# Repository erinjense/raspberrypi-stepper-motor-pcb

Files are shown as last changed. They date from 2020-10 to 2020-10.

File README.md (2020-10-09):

# Quad Stepper Motor Driver, Printed Circuit Board

## Disclaimer

This repository, "raspberrypi-stepper-motor-pcb", includes Open Source Hardware "DESGIN FILES AND GUIDES".

THE "DESIGN FILES AND GUIDES" ARE PROVIDED “AS IS”, WITHOUT WARRANTY OF ANY KIND, EXPRESS OR IMPLIED, INCLUDING BUT NOT LIMITED TO THE WARRANTIES OF MERCHANTABILITY, FITNESS FOR A PARTICULAR PURPOSE AND NONINFRINGEMENT. IN NO EVENT SHALL THE AUTHORS OR COPYRIGHT HOLDERS BE LIABLE FOR ANY CLAIM, DAMAGES OR OTHER LIABILITY, WHETHER IN AN ACTION OF CONTRACT, TORT OR OTHERWISE, ARISING FROM, OUT OF OR IN CONNECTION WITH THE "DESIGN FILES AND GUIDES" OR THE USE OR OTHER DEALINGS IN THE "DESIGN FILES AND GUIDES".

See [LICENSE](./LICENSE.md) for further details.

NOTE: This is not a Raspberry Pi "HAT" (Hardware Attached Top). A Raspberry Pi "HAT" is a specification by the Raspberry Pi Foundation set out to ensure various modules designed to interface with the Raspberry Pi do not conflict with each other. It is up to the User to ensure that the GPIO pins within this PCB module does not conflict with other modules, "HAT"s or desired use-cases.

See more within: [Raspberry Pi HAT Details](https://github.com/raspberrypi/hats)

This device is under test and not guaranteed to operate within electrical specifications or desired functionality.

##  Device Overview

### Features
✔️ Interfaces to Raspberry Pi, single-board computer, 40W GPIO Connector.

✔️ Drives up to 4 Stepper Motors.

✔️ Step Mode Control Switches.
 - Full, 1/2, 1/4, and 1/8

✔️ Motor Drive Current Limiting Potentiometers.

✔️ Mixed Decay Mode.

✔️ Minimal Raspberry Pi GPIO Pin Usage
-  Pins: 11, 13, 15, 29, 31 

✔️ DC Barrel Jack for commonly available power supplies.

### Electrical Specifications
✔️ VM Motor Power Supply (DC barrel jack): 8 ~ 32V

✔️ Continuous Motor Output Current: 0 ~ 1.5 A / Motor Set

✔️ Working Temperature: TBD

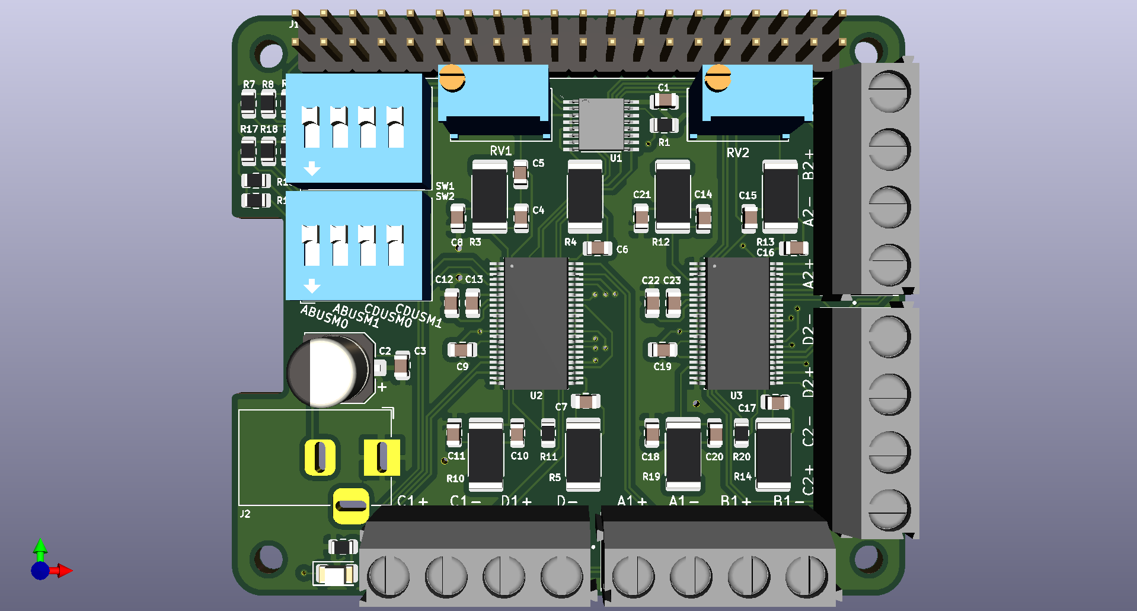
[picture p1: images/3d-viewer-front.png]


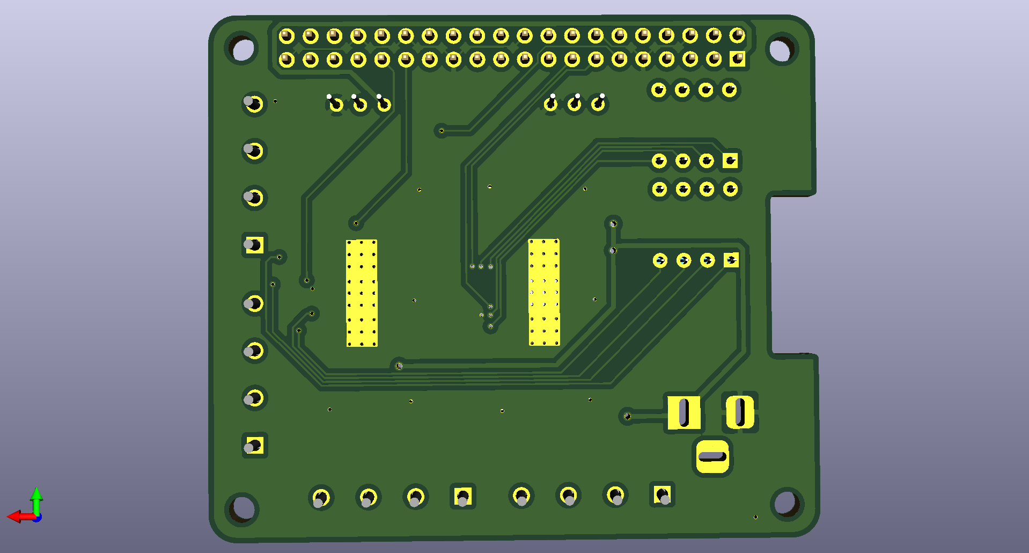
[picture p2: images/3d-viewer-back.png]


## Guides
- [Motor Selection](#motor-selection-guide)
- [Device Operation](#device-operation-guide)
- [Ordering PCB](#jlcpcb-order-guide)

## Motor Selection Guide
Coming soon...

## Device Operation Guide
Coming soon...

## Ordering Guide
This order guide covers the following:

- Purchasing printed circuit boards from JLCPCB with SMT assembly.
- Ordering remaining, through-hole, components from LCSC.

### Step 1: Upload Gerber Files
 - Download or clone this repository onto your computer.
 - Go to [JLCPCB.com](https://jlcpcb.com/)
 - Select "Quote Now" on the right-hand of JLCPCB.

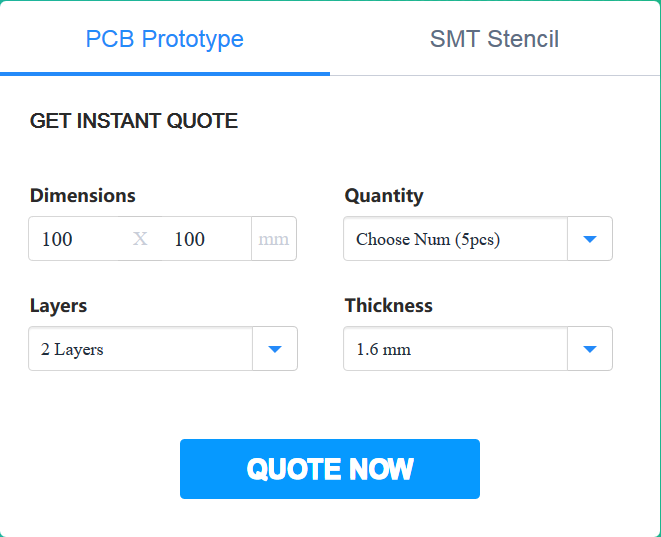
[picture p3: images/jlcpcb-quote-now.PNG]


- Select "Add your gerber file" on JLCPCB.
- Locate the "gerber" directory within this repository on your computer.
- Select and upload "gerber.zip".

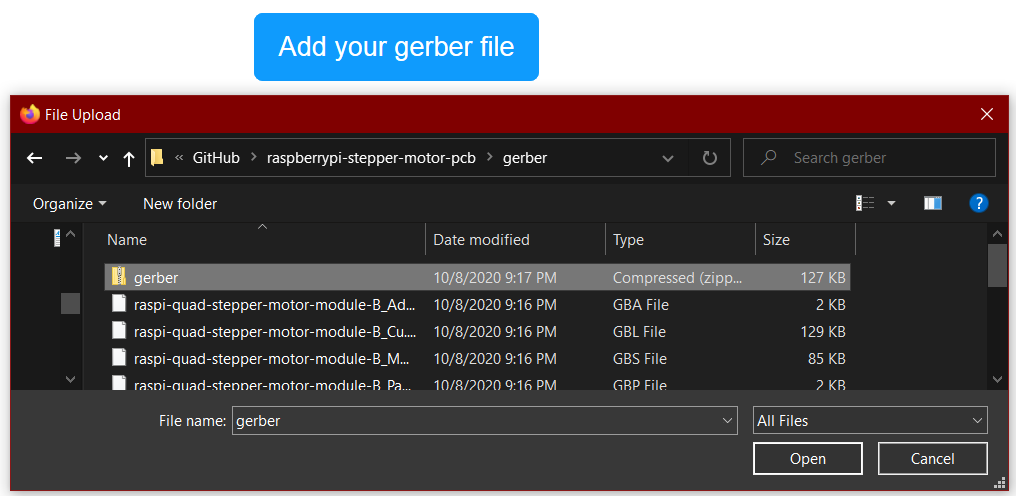
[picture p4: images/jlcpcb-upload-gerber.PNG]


### Step 2: Confirm PCB Specifications
- Confirm the following optional PCB specifications:
    - PCB Qty
    - Surface Finish (Lead-Free is extra money, but I chose this option.)
- Leave remaining options default unless you have a reason to change.

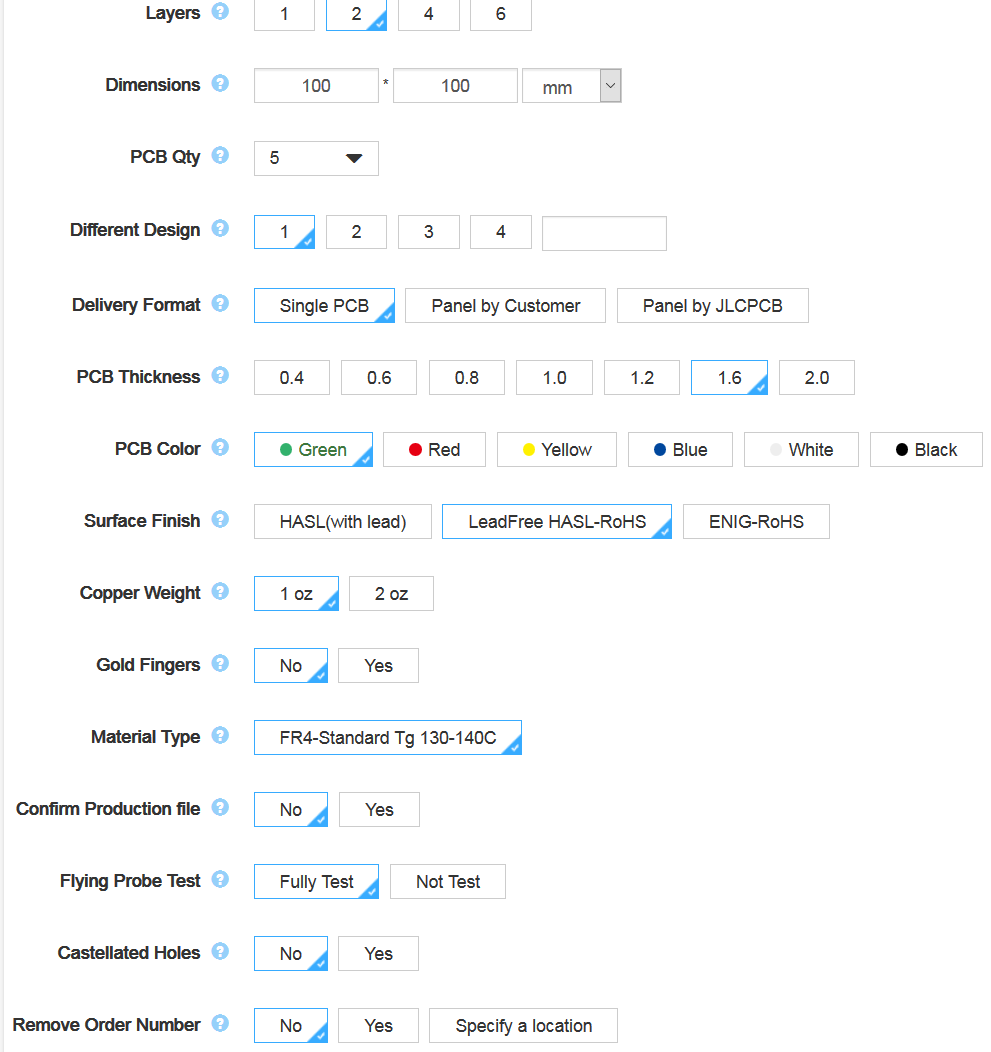
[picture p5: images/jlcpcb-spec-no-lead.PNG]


### Step 3: Optional SMT Assembly
- Toggle "SMT Assembly" option.
- Select "Assemble top side".
- Select your "SMT Qty" preference. (5 vs. 2)
- Leave Tooling holes as: "Added by JLCPCB".
- Click "Confirm".

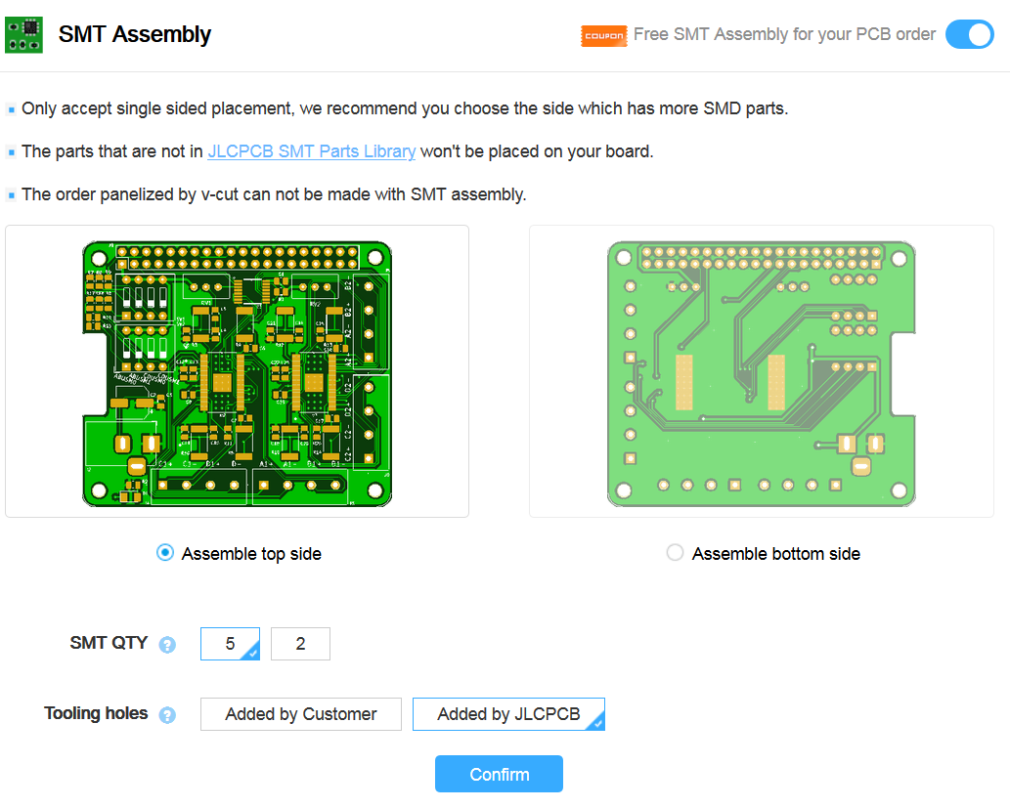
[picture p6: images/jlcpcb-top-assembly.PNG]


- ### Upload BOM and CPL
    - Click "Add BOM File".
    - Go to the "assembly" directory within the repository location on your computer.
    - Select "raspi-quad-stepper-motor-module_bom_jlc.csv"
    - Click "Add CPL File".
    - Go to the "assembly" directory within the repository location on your computer.
    - Select "raspi-quad-stepper-motor-module_cpl_jlc.csv"

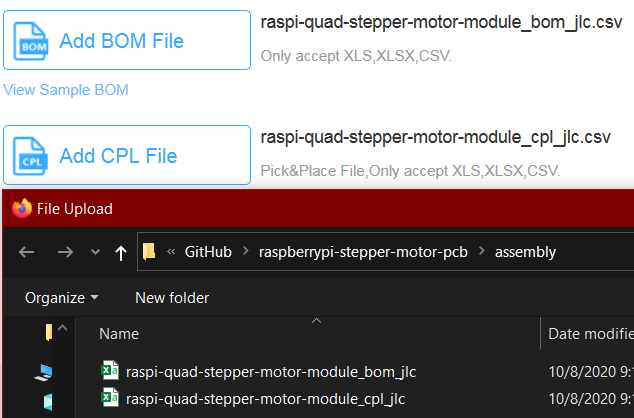
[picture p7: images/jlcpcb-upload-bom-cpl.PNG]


### Step 4: Review Charge Details
- If you chose "SMT assembly" you will see the SMT devices that will be populated on the boards.

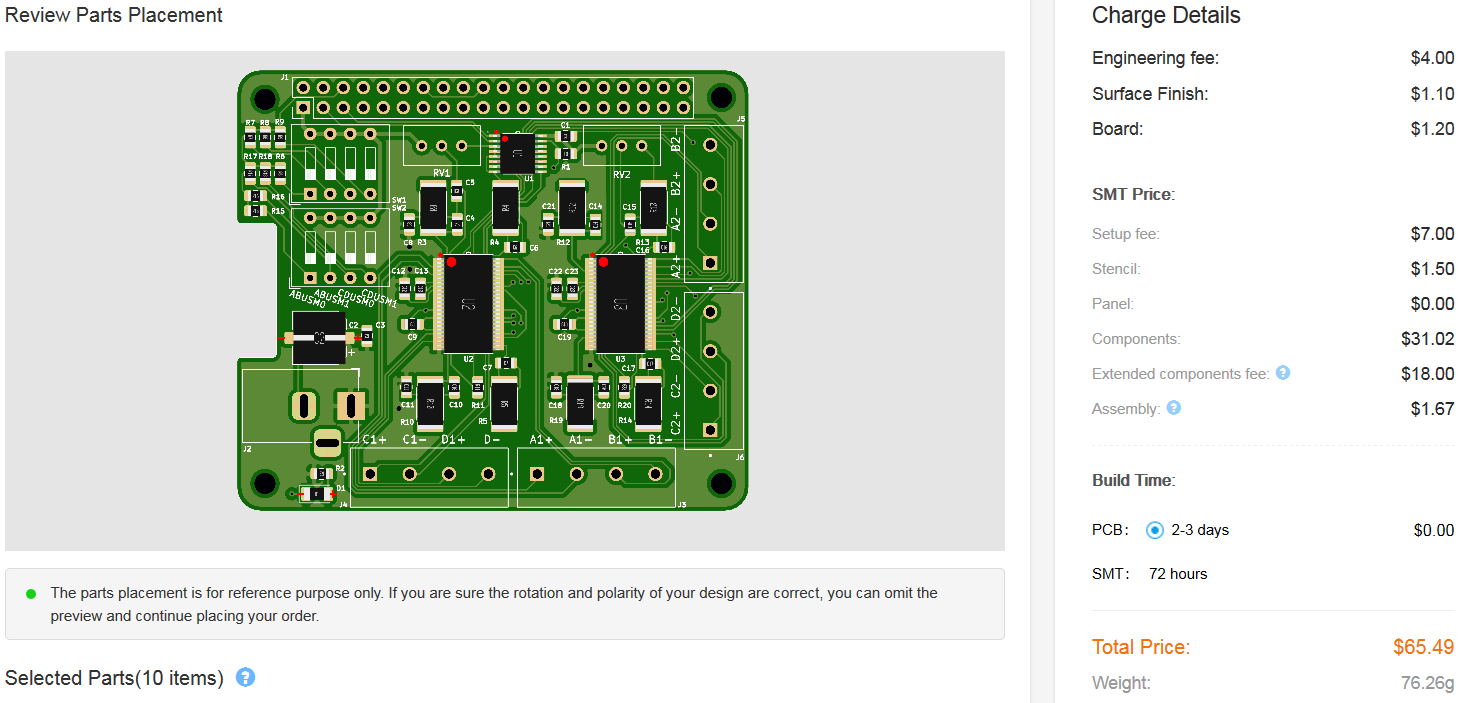
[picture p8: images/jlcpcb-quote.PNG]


- Notice that the through-hole components will still need to be ordered and soldered by hand.

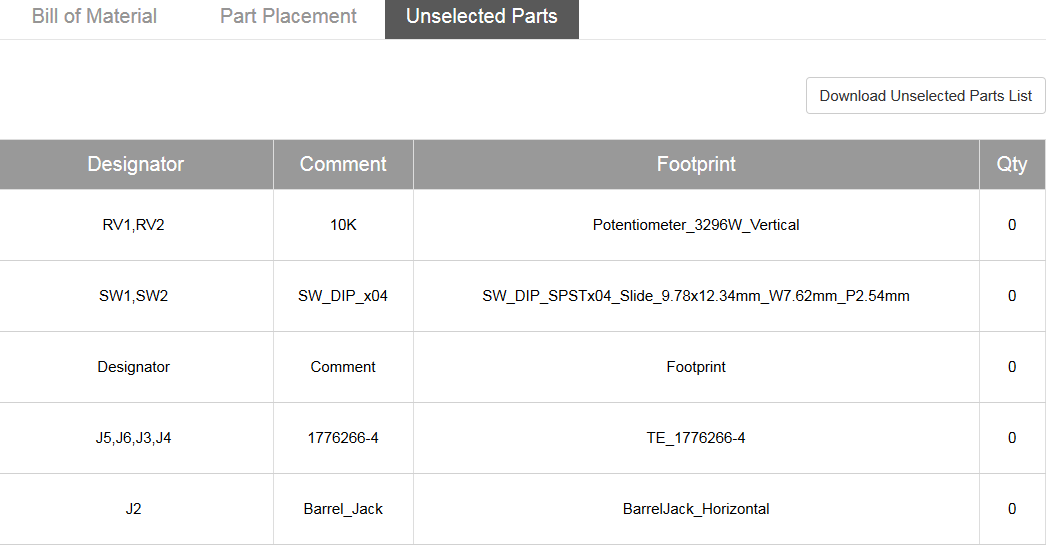
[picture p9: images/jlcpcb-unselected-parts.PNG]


### Step 5: Purchase Remaining Components on LCSC

### Upload Through Hole BOM
- Go to [LCSC.com](https://lcsc.com/)
- Select "BOM Tool" within the LCSC banner.
- Upload BOM File by choosing "select a file" on LCSC.
- Go to the "assembly" directory within this repository on your computer.
- Select "raspi-quad-stepper-motor-module_bom_through_hole_lcsc.xlsx"

NOTE: If you did not choose SMT assembly on JLCPCB, you will have to order all the components, not just the through-hole parts, by uploading the "raspi-quad-stepper-motor-module_bom_jlc.csv" instead of "raspi-quad-stepper-motor-module_bom_through_hole_lcsc.xlsx".

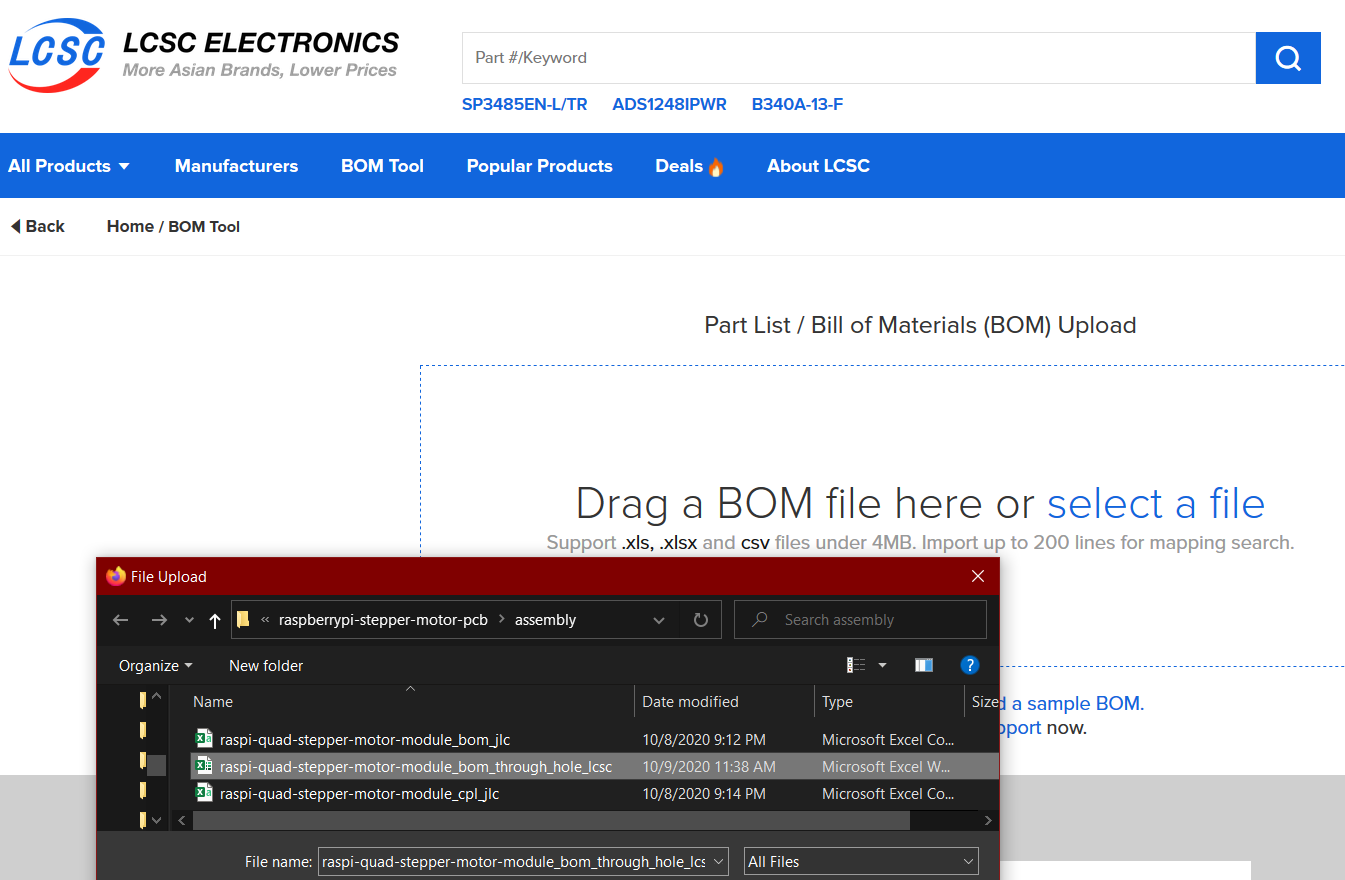
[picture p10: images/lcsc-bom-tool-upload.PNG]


### Select BOM Column Types
- Locate the "LCSC Part Number" column.
- Select "LCSC Part Number" from the above drop-down box.
- Locate the "Quantity" column.
- Select "Quantity" from the above drop-down box.
- Leave remaining columns as "select type".

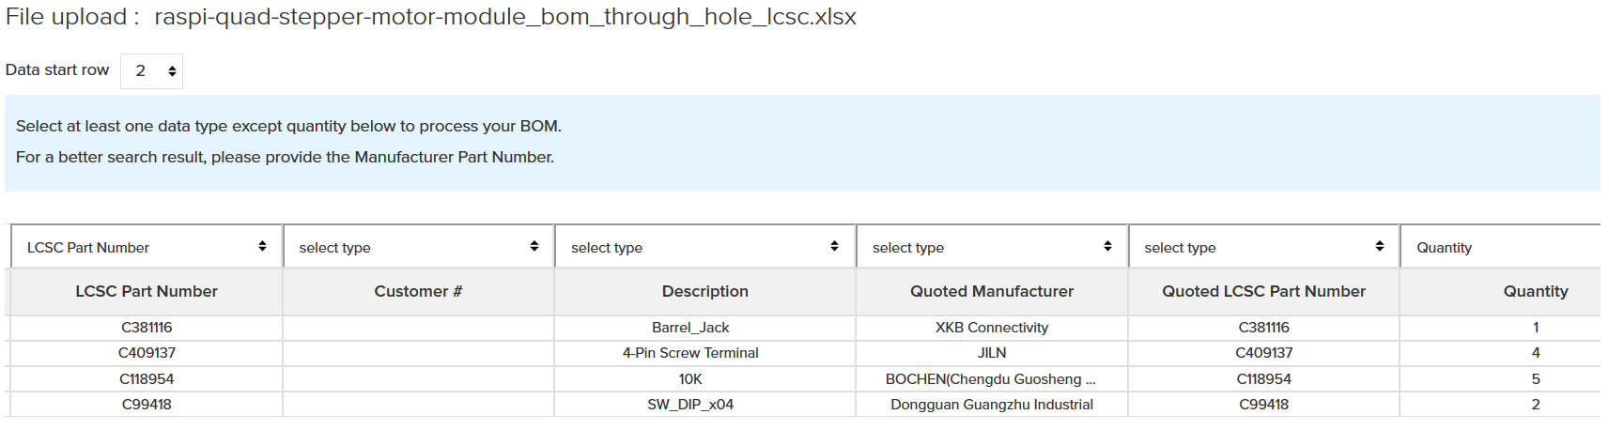
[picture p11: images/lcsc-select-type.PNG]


### Step 6: Confirm Purchases
- Confirm your JLCPCB order.
- Confirm your LCSC order.

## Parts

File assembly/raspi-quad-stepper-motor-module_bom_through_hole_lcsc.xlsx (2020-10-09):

LCSC Part Number | Customer # | Description | Quoted Manufacturer | Quoted LCSC Part Number | Quantity | Unit Price | Quantity Available | Min\Mult Order Qty | RoHS | Part Match Confidence
C381116 |  | Barrel_Jack | XKB Connectivity | C381116 | 1 | 0.183217 | 5441 | 1\1 | yes | 100%
C409137 |  | 4-Pin Screw Terminal | JILN | C409137 | 4 | 0.140633 | 3609 | 1\1 | yes | 100%
C118954 |  | 10K | BOCHEN(Chengdu Guosheng Tech) | C118954 | 5 | 0.127617 | 72020 | 5\5 | yes | 100%
C99418 |  | SW_DIP_x04 | Dongguan Guangzhu Industrial | C99418 | 2 | 0.178283 | 29665 | 1\1 | yes | 100%

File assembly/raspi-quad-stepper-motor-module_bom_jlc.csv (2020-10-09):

Comment | Designator | Footprint | LCSC Part #
100nF | C1,C4,C6,C7,C10,C5,C8,C11,C12,C14,C16,C17,C20,C15,C18,C21,C22 | C_0805_2012Metric | C28233
100uF | C2 | CP_Elec_6.3x7.7 | C249983
100nF | C3 | C_0805_2012Metric | C28233
470nF | C9,C19 | C_0805_2012Metric | C13967
10nF | C13,C23 | C_0805_2012Metric | C1710
LED | D1 | LED_1206_3216Metric | C84270
Barrel_Jack | J2 | BarrelJack_Horizontal | C381116
1776266-4 | J5,J6,J3,J4 | TE_1776266-4 | C409137
10K | R1,R9,R8,R7,R6,R11,R18,R17,R16,R15,R20 | R_0805_2012Metric | C17414
R_2.2K | R2 | R_0805_2012Metric | C17520
0.2 | R3,R4,R5,R10,R12,R13,R14,R19 | R_2512_6332Metric | C76258
10K | RV1,RV2 | Potentiometer_3296W_Vertical | C118954
SW_DIP_x04 | SW1,SW2 | SW_DIP_SPSTx04_Slide_9.78x12.34mm_W7.62mm_P2.54mm | C99418
PCA9557PW,118 | U1 | SOP65P640X110-16N | C141380
DRV8821DCAR | U2,U3 | SOP50P810X120-49N | C81564

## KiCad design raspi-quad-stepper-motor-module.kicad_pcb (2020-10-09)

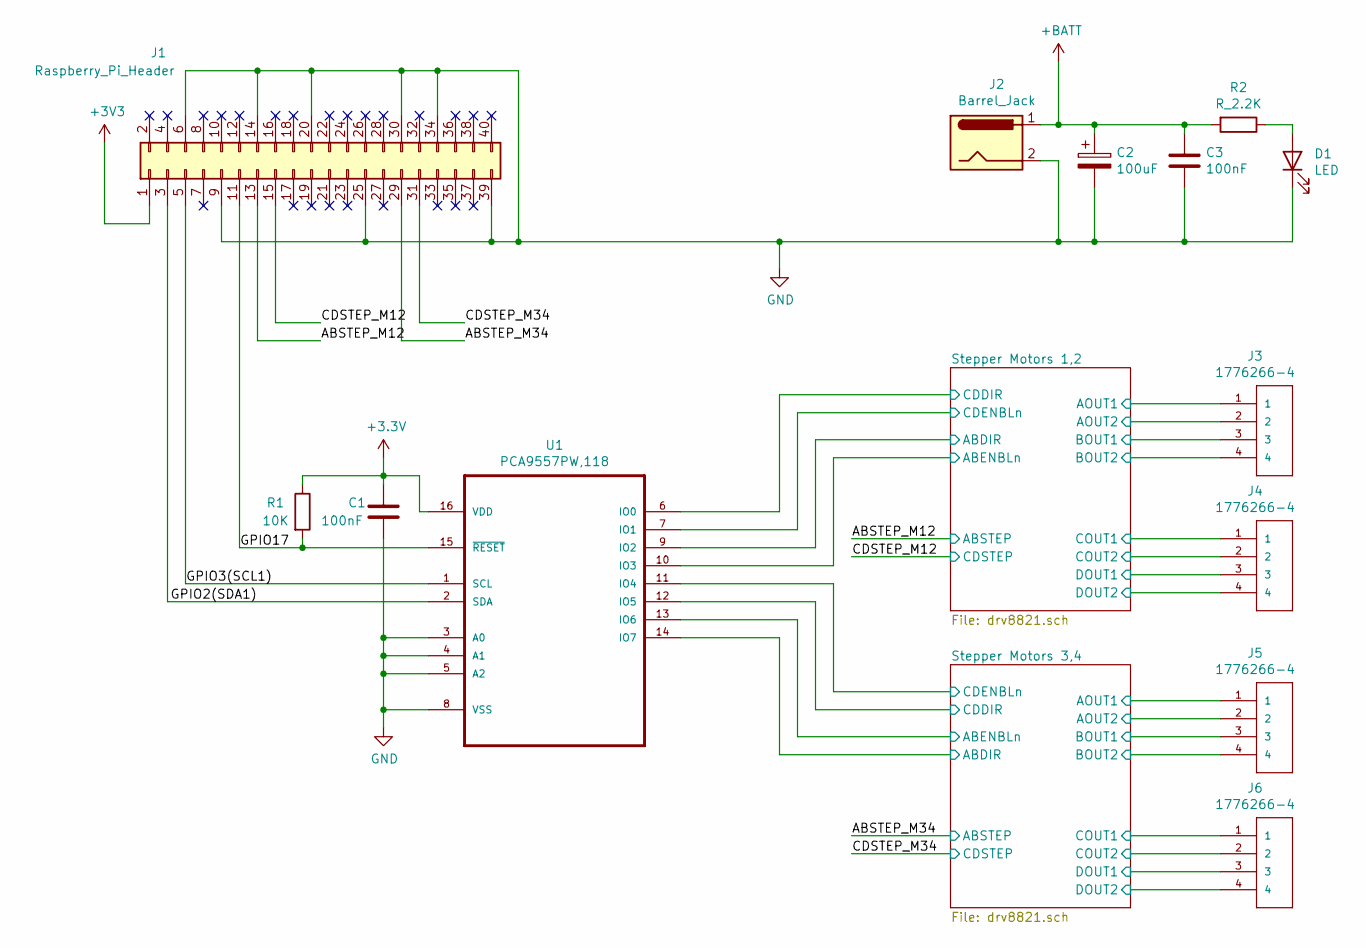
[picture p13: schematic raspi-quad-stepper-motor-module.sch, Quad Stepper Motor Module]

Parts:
C1, C3: 100nF; C_0805_2012Metric; LCSC C28233
C2: 100uF; CP_Elec_6.3x7.7; LCSC C249983
D1: LED; LED_1206_3216Metric; LCSC C84270
J1: Raspberry_Pi_Header; PinHeader_2x20_P2.54mm_Vertical
J2: Barrel_Jack; BarrelJack_Horizontal; LCSC C381116
J3, J4, J5, J6: 1776266-4; TE_1776266-4; LCSC C409137
R1: 10K; R_0805_2012Metric; LCSC C17414
R2: R_2.2K; R_0805_2012Metric; LCSC C17520
U1: PCA9557PW,118; SOP65P640X110-16N; LCSC C141380

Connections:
+BATT: C2.1, C3.1, J2.1, R2.2; also elsewhere on the board
/ABSTEP_M12: J1.13; also elsewhere on the board
/ABSTEP_M34: J1.29; also elsewhere on the board
/CDSTEP_M12: J1.15; also elsewhere on the board
/CDSTEP_M34: J1.31; also elsewhere on the board
/GPIO2(SDA1): J1.3, U1.2 (SDA)
/GPIO3(SCL1): J1.5, U1.1 (SCL)
/GPIO17: J1.11, R1.2, U1.15 (~RESET)
/Stepper Motors 1,2/ABDIR: U1.9 (IO2); also elsewhere on the board
/Stepper Motors 1,2/ABENBLn: U1.10 (IO3); also elsewhere on the board
/Stepper Motors 1,2/AOUT1: J3.1; also elsewhere on the board
/Stepper Motors 1,2/AOUT2: J3.2; also elsewhere on the board
/Stepper Motors 1,2/BOUT1: J3.3; also elsewhere on the board
/Stepper Motors 1,2/BOUT2: J3.4; also elsewhere on the board
/Stepper Motors 1,2/CDDIR: U1.6 (IO0); also elsewhere on the board
/Stepper Motors 1,2/CDENBLn: U1.7 (IO1); also elsewhere on the board
/Stepper Motors 1,2/COUT1: J4.1; also elsewhere on the board
/Stepper Motors 1,2/COUT2: J4.2; also elsewhere on the board
/Stepper Motors 1,2/DOUT1: J4.3; also elsewhere on the board
/Stepper Motors 1,2/DOUT2: J4.4; also elsewhere on the board
/Stepper Motors 3,4/ABDIR: U1.14 (IO7); also elsewhere on the board
/Stepper Motors 3,4/ABENBLn: U1.13 (IO6); also elsewhere on the board
/Stepper Motors 3,4/AOUT1: J5.1; also elsewhere on the board
/Stepper Motors 3,4/AOUT2: J5.2; also elsewhere on the board
/Stepper Motors 3,4/BOUT1: J5.3; also elsewhere on the board
/Stepper Motors 3,4/BOUT2: J5.4; also elsewhere on the board
/Stepper Motors 3,4/CDDIR: U1.12 (IO5); also elsewhere on the board
/Stepper Motors 3,4/CDENBLn: U1.11 (IO4); also elsewhere on the board
/Stepper Motors 3,4/COUT1: J6.1; also elsewhere on the board
/Stepper Motors 3,4/COUT2: J6.2; also elsewhere on the board
/Stepper Motors 3,4/DOUT1: J6.3; also elsewhere on the board
/Stepper Motors 3,4/DOUT2: J6.4; also elsewhere on the board
GND: C1.2, C2.2, C3.2, D1.1 (K), J1.6, J1.9, J1.14, J1.20, J1.25, J1.30, J1.34, J1.39, J2.2, U1.3 (A0), U1.4 (A1), U1.5 (A2), U1.8 (VSS); also elsewhere on the board
unnamed: D1.2 (A), R2.1

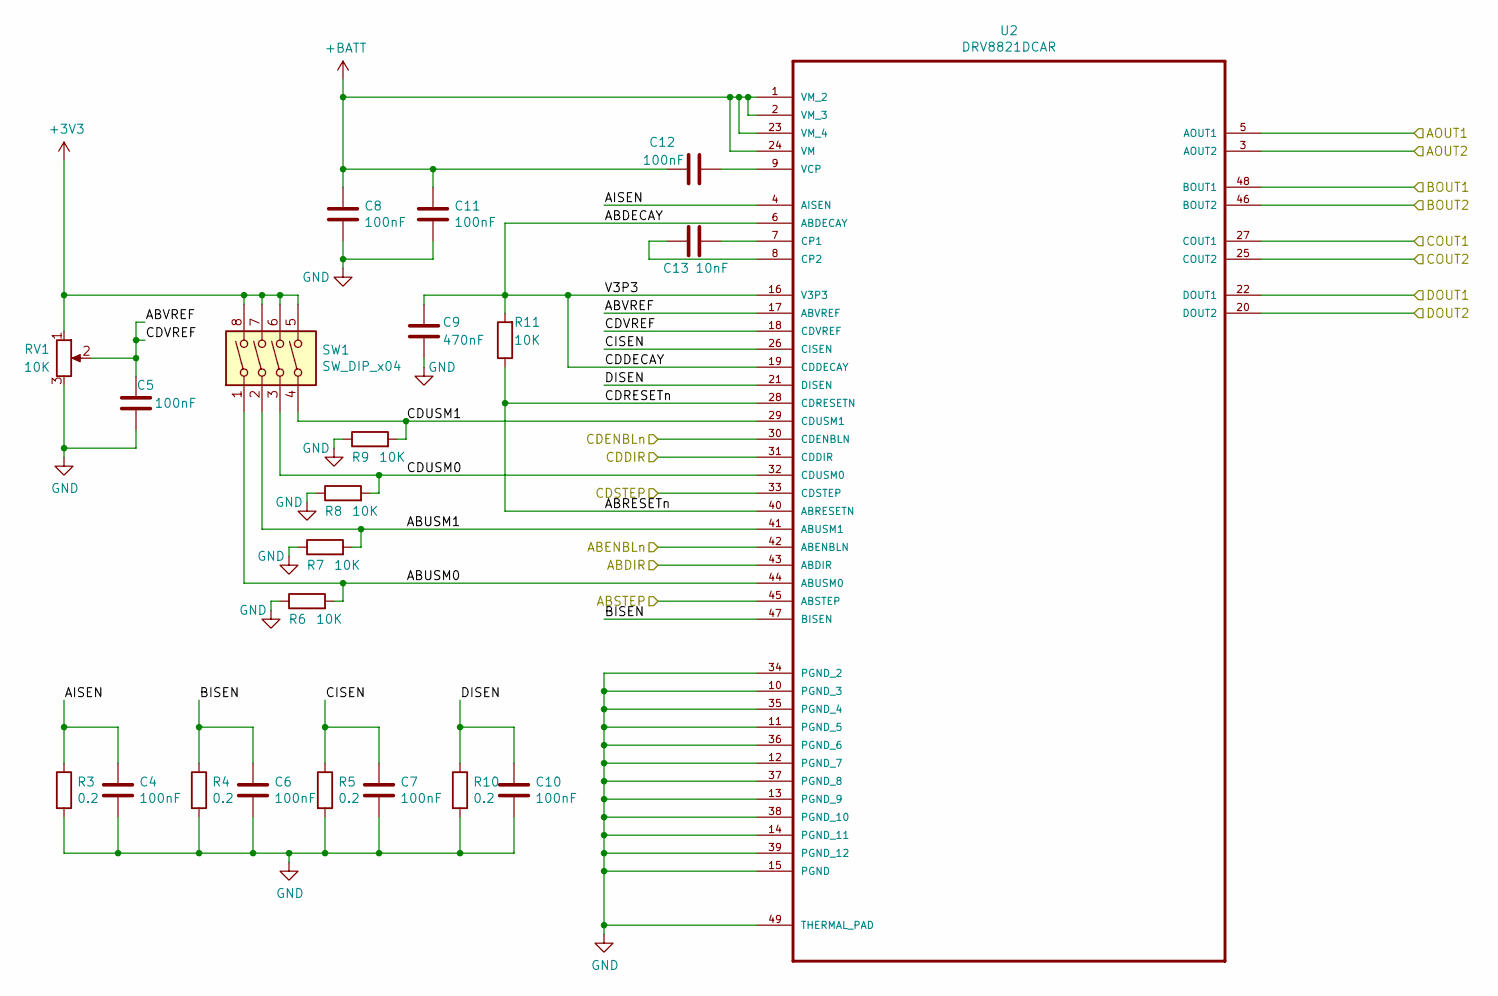
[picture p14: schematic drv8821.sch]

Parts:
C4, C5, C6, C7, C8, C10, C11, C12: 100nF; C_0805_2012Metric; LCSC C28233
C9: 470nF; C_0805_2012Metric; LCSC C13967
C13: 10nF; C_0805_2012Metric; LCSC C1710
R3, R4, R5, R10: 0.2; R_2512_6332Metric; LCSC C76258
R6, R7, R8, R9, R11: 10K; R_0805_2012Metric; LCSC C17414
RV1: 10K; Potentiometer_3296W_Vertical; LCSC C118954
SW1: SW_DIP_x04; SW_DIP_SPSTx04_Slide_9.78x12.34mm_W7.62mm_P2.54mm; LCSC C99418
U2: DRV8821DCAR; SOP50P810X120-49N; LCSC C81564

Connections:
+BATT: C8.1, C11.1, C12.1, U2.1 (VM_2), U2.2 (VM_3), U2.23 (VM_4), U2.24 (VM); also elsewhere on the board
/ABSTEP_M12: U2.45 (ABSTEP); also elsewhere on the board
/CDSTEP_M12: U2.33 (CDSTEP); also elsewhere on the board
/Stepper Motors 1,2/ABDECAY: C9.1, R11.2, U2.6 (ABDECAY), U2.16 (V3P3), U2.19 (CDDECAY)
/Stepper Motors 1,2/ABDIR: U2.43 (ABDIR); also elsewhere on the board
/Stepper Motors 1,2/ABENBLn: U2.42 (ABENBLN); also elsewhere on the board
/Stepper Motors 1,2/ABRESETn: R11.1, U2.28 (CDRESETN), U2.40 (ABRESETN)
/Stepper Motors 1,2/ABUSM0: R6.2, SW1.1, U2.44 (ABUSM0)
/Stepper Motors 1,2/ABUSM1: R7.2, SW1.2, U2.41 (ABUSM1)
/Stepper Motors 1,2/ABVREF: C5.1, RV1.2, U2.17 (ABVREF), U2.18 (CDVREF)
/Stepper Motors 1,2/AISEN: C4.1, R3.1, U2.4 (AISEN)
/Stepper Motors 1,2/AOUT1: U2.5 (AOUT1); also elsewhere on the board
/Stepper Motors 1,2/AOUT2: U2.3 (AOUT2); also elsewhere on the board
/Stepper Motors 1,2/BISEN: C6.1, R4.1, U2.47 (BISEN)
/Stepper Motors 1,2/BOUT1: U2.48 (BOUT1); also elsewhere on the board
/Stepper Motors 1,2/BOUT2: U2.46 (BOUT2); also elsewhere on the board
/Stepper Motors 1,2/CDDIR: U2.31 (CDDIR); also elsewhere on the board
/Stepper Motors 1,2/CDENBLn: U2.30 (CDENBLN); also elsewhere on the board
/Stepper Motors 1,2/CDUSM0: R8.2, SW1.3, U2.32 (CDUSM0)
/Stepper Motors 1,2/CDUSM1: R9.2, SW1.4, U2.29 (CDUSM1)
/Stepper Motors 1,2/CISEN: C7.1, R5.1, U2.26 (CISEN)
/Stepper Motors 1,2/COUT1: U2.27 (COUT1); also elsewhere on the board
/Stepper Motors 1,2/COUT2: U2.25 (COUT2); also elsewhere on the board
/Stepper Motors 1,2/DISEN: C10.1, R10.1, U2.21 (DISEN)
/Stepper Motors 1,2/DOUT1: U2.22 (DOUT1); also elsewhere on the board
/Stepper Motors 1,2/DOUT2: U2.20 (DOUT2); also elsewhere on the board
GND: C4.2, C5.2, C6.2, C7.2, C8.2, C9.2, C10.2, C11.2, R3.2, R4.2, R5.2, R6.1, R7.1, R8.1, R9.1, R10.2, RV1.3, U2.10 (PGND_3), U2.11 (PGND_5), U2.12 (PGND_7), U2.13 (PGND_9), U2.14 (PGND_11), U2.15 (PGND), U2.34 (PGND_2), U2.35 (PGND_4), U2.36 (PGND_6), U2.37 (PGND_8), U2.38 (PGND_10), U2.39 (PGND_12), U2.49 (THERMAL_PAD); also elsewhere on the board
unnamed: C12.2, U2.9 (VCP)
unnamed: C13.1, U2.7 (CP1)
unnamed: C13.2, U2.8 (CP2)

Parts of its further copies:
C14, C15, C16, C17, C18, C20, C21, C22: 100nF; C_0805_2012Metric; LCSC C28233
C19: 470nF; C_0805_2012Metric; LCSC C13967
C23: 10nF; C_0805_2012Metric; LCSC C1710
R12, R13, R14, R19: 0.2; R_2512_6332Metric; LCSC C76258
R15, R16, R17, R18, R20: 10K; R_0805_2012Metric; LCSC C17414
RV2: 10K; Potentiometer_3296W_Vertical; LCSC C118954
SW2: SW_DIP_x04; SW_DIP_SPSTx04_Slide_9.78x12.34mm_W7.62mm_P2.54mm; LCSC C99418
U3: DRV8821DCAR; SOP50P810X120-49N; LCSC C81564

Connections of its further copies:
+BATT: C18.1, C21.1, C22.1, U3.1 (VM_2), U3.2 (VM_3), U3.23 (VM_4), U3.24 (VM); also elsewhere on the board
/ABSTEP_M34: U3.45 (ABSTEP); also elsewhere on the board
/CDSTEP_M34: U3.33 (CDSTEP); also elsewhere on the board
/Stepper Motors 3,4/ABDECAY: C19.1, R20.2, U3.6 (ABDECAY), U3.16 (V3P3), U3.19 (CDDECAY)
/Stepper Motors 3,4/ABDIR: U3.43 (ABDIR); also elsewhere on the board
/Stepper Motors 3,4/ABENBLn: U3.42 (ABENBLN); also elsewhere on the board
/Stepper Motors 3,4/ABRESETn: R20.1, U3.28 (CDRESETN), U3.40 (ABRESETN)
/Stepper Motors 3,4/ABUSM0: R15.2, SW2.1, U3.44 (ABUSM0)
/Stepper Motors 3,4/ABUSM1: R16.2, SW2.2, U3.41 (ABUSM1)
/Stepper Motors 3,4/ABVREF: C15.1, RV2.2, U3.17 (ABVREF), U3.18 (CDVREF)
/Stepper Motors 3,4/AISEN: C14.1, R12.1, U3.4 (AISEN)
/Stepper Motors 3,4/AOUT1: U3.5 (AOUT1); also elsewhere on the board
/Stepper Motors 3,4/AOUT2: U3.3 (AOUT2); also elsewhere on the board
/Stepper Motors 3,4/BISEN: C16.1, R13.1, U3.47 (BISEN)
/Stepper Motors 3,4/BOUT1: U3.48 (BOUT1); also elsewhere on the board
/Stepper Motors 3,4/BOUT2: U3.46 (BOUT2); also elsewhere on the board
/Stepper Motors 3,4/CDDIR: U3.31 (CDDIR); also elsewhere on the board
/Stepper Motors 3,4/CDENBLn: U3.30 (CDENBLN); also elsewhere on the board
/Stepper Motors 3,4/CDUSM0: R17.2, SW2.3, U3.32 (CDUSM0)
/Stepper Motors 3,4/CDUSM1: R18.2, SW2.4, U3.29 (CDUSM1)
/Stepper Motors 3,4/CISEN: C17.1, R14.1, U3.26 (CISEN)
/Stepper Motors 3,4/COUT1: U3.27 (COUT1); also elsewhere on the board
/Stepper Motors 3,4/COUT2: U3.25 (COUT2); also elsewhere on the board
/Stepper Motors 3,4/DISEN: C20.1, R19.1, U3.21 (DISEN)
/Stepper Motors 3,4/DOUT1: U3.22 (DOUT1); also elsewhere on the board
/Stepper Motors 3,4/DOUT2: U3.20 (DOUT2); also elsewhere on the board
GND: C14.2, C15.2, C16.2, C17.2, C18.2, C19.2, C20.2, C21.2, R12.2, R13.2, R14.2, R15.1, R16.1, R17.1, R18.1, R19.2, RV2.3, U3.10 (PGND_3), U3.11 (PGND_5), U3.12 (PGND_7), U3.13 (PGND_9), U3.14 (PGND_11), U3.15 (PGND), U3.34 (PGND_2), U3.35 (PGND_4), U3.36 (PGND_6), U3.37 (PGND_8), U3.38 (PGND_10), U3.39 (PGND_12), U3.49 (THERMAL_PAD); also elsewhere on the board
unnamed: C22.2, U3.9 (VCP)
unnamed: C23.1, U3.7 (CP1)
unnamed: C23.2, U3.8 (CP2)

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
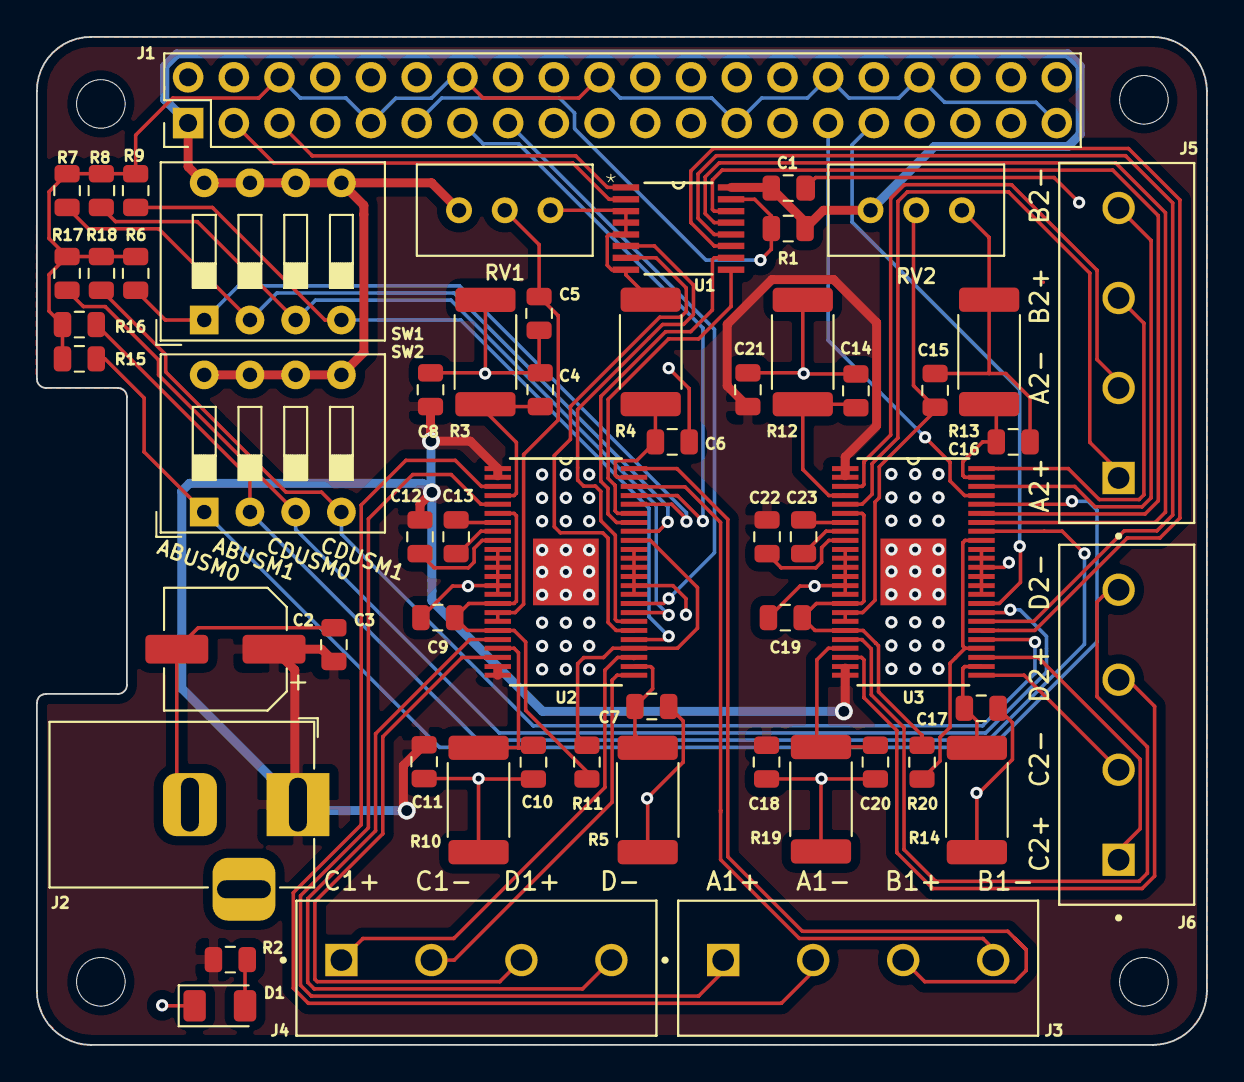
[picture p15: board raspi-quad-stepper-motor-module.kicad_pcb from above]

Board: 2 copper layers, 65.0 x 56.0 mm, 61 parts (0 on the bottom side), 63 nets.

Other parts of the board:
MK1, MK2, MK3, MK4: M2.5; MountingHole_2.7mm_M2.5

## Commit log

2020-10-09 Initial Commit
    Revision A.
    [drv8821.sch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]
2020-10-09 Updated README and LICENSE.
    Added Order Guide and updated usage disclaimer.
    [raspi-quad-stepper-motor-module_bom_through_hole_lcsc.xlsx]
